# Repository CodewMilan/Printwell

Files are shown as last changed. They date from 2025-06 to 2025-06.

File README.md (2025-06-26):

# Core3D

Core3D is an open-source, budget-friendly CoreXY 3D printer designed for makers who want speed, rigidity,

---

## What’s Inside

CoreXY motion system  
Linear rails on all axes  
Steel + 2020 extrusion frame  
Klipper firmware ready  
Custom-printed brackets and mounts  
BLTouch for mesh leveling  
Fast print speeds on 24V

---

## Sample BOM

Here’s a quick look at some of the core components:

| Component | Description | Qty | Price (PHP) | Price (USD) | Price (INR) |
|---|---|-----|---|---|---|
| Linear Rails | At Least 320mm (THK RSH12ZM) | 3 | 690.00 | $12.07 | 1041.90 |
| Z-Axis Ball Screw Actuator Rail | SG2602A-250H | 1 | 6000.00 | $104.97 | 9060.00 |
| BTT SKR Mini E3 V3 | 3D Printer Controller (32bit) | 1 | 2027.00 | $35.46 | 3060.77 |
| FYSTEC Mini12864 RGB LCD | RGB Neopixel Backlit LCD for 3D Printers | 1 | 393.00 | $6.88 | 593.43 |
| Stepper Motors (NEMA 17, 48mm)  | 3D Printer's Motors (w/ Cables) | 4 | 267.00 | $4.67 | 403.17 |
| 24V 16.7A 400W Power Supply | A compact PSU | 1 | 475.00 | $8.31 | 717.25 |
| Dual Gear Drive Extruder (Clone)| Bontech dual gear extruder clone | 1 | 318.00 | $5.56 | 480.18 |
| Capricorn PTFE Tube (Set) | PTFE Tube for Bowden setups | 1 | 176.00 | $3.08 | 265.76 |
| Heatbed (Ender 3) | 235x235 24V Ender 3 Heatbed | 1 | 875.00 | $15.31 | 1321.25 |
| Heatbed Knob Set | Bolts & nuts for the heatbed | 1 | 132.00 | $2.31 | 199.32 |
| V6 Hotend Set (E3D Clone) | Classic standard hotend | 1 | 343.00 | $6.00 | 517.93 |
| V6 Hotend Aluminum Bracket | Bracket for the V6 Hotend | 1 | 101.00 | $1.77 | 152.51 |
| CHT 0.4mm Nozzle (Clone) | High-speed nozzle upgrade | 1 | 205.00 | $3.59 | 309.55 |
| Endstop Limit Switches | Standard limit switch | 3 | 85.00 | $1.49 | 128.35 |
| 4010 24V Cooling Fan | Blower fan for part cooling | 1 | 92.00 | $1.61 | 138.92 |
| GT2 Timing Belt (Set) | 3m belt set for 3D printers | 2 | 90.00 | $1.57 | 135.90 |
| 20T Stepper Pulley (GT2) | For 5mm shaft steppers | 2 | 44.00 | $0.77 | 66.44 |
| 16T Idler Pulley (GT2) | CoreXY pulley, 3mm bore | 6 | 34.00 | $0.59 | 51.34 |
| 16T Smooth Idler Pulley (GT2) | CoreXY pulley, 3mm bore | 2 | 41.00 | $0.72 | 61.91 |
| 5mm Coupler | For Z Rail and NEMA 17 | 1 | 29.00 | $0.51 | 43.79 |
| M3 Threaded Heat Insert Set | For metal threads in plastic | 1 | 131.00 | $2.29 | 197.81 |
| M3 Washer Set | Basic M3 washers | 1 | 18.00 | $0.31 | 27.18 |
| 1x1" Steel Tubular | 6m of 1x1" steel tubing | 1 | 220.00 | $3.85 | 332.20 |
| 1" Steel Flatbar | 6m of 3mm thick flat steel | 1 | 150.00 | $2.62 | 226.50 |
| 2020 Aluminum Profile | 320mm extrusion | 1 | 196.00 | $3.43 | 295.96 |
| 2020 M3 T-Slot Nuts (Set) | M3 nuts for 2020 extrusion | 1 | 54.00 | $0.94 | 81.54 |
| Generic ABS Filament | ABS spool | 1 | 550.00 | $9.62 | 830.50 |
| TriangleLabs Volcano CHC Hotend | High speed 120W hotend | 1 | 1594.00 | $27.89 | 2406.94 |
| 0.4mm Volcano CHT Nozzle | High-flow nozzle for Volcano | 1 | 123.00 | $2.15 | 185.73 |
| BL-Touch Bed Levelling Sensor | For mesh leveling | 1 | 561.00 | $9.81 | 847.11 |
| PowerHouse Mig Welder | Budget IGBT MIG welder | 1 | 5580.00 | $97.62 | 8425.80 |
| Travon 7" Cutoff Tool | Budget cut-off tool | 1 | 2365.00 | $41.38 | 3571.15 |
| Hand Tap Set | For threading metal | 1 | 173.00 | $3.03 | 261.23 |

**Subtotal:** $305.14

---

## Firmware

Core3D runs on **Klipper** for speed and precision.

---

## pictures

 
 


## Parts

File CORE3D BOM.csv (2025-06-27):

3D Printer Components |  |  |  |  |  |  | x
Component | Description | Qty | Price (PHP) | Price (USD) | Link 1: | Price (INR) | x
Linear Rails | At Least 320mm (THK RSH12ZM) | 3 | 690.00 | $12.07 | https://www.e-gizmo.net/ | 1041.9 | x
Z-Axis Ball Screw Actuator Rail | SG2602A-250H | 1 | 6,000.00 | $104.97 | https://www.e-gizmo.net/ | 9060 | x
BTT SKR Mini E3 V3 | 3D Printer Controller (32bit) | 1 | 2,027.00 | $35.46 | https://shopee.ph/BIGTREETECH-BTT-SKR-MINI-E3-V3.0-32-Bit-Motherboard-Onboard-TMC2209-UART-3D-Printer-Parts-for-Ender3-Ender5-CR10-3D-Printer-i.367074809.2095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 | 3060.77 | x
FYSTEC Mini12864 RGB LCD | RGB Neopixel Backlit LCD for 3D Printers | 1 | 393.00 | $6.88 | https://shopee.ph/S-Mini12864-V3.0-12864-GLCD-Liquid-Crystal-Screen-Mini-Lcd12864-Display-Controller-3D-Printer-LCD-M-i.1144147547.25758436024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 | 593.43 | x
Stepper Motors (NEMA 17, 48mm) | 3D Printer's Motors (w/ Cables) | 4 | 267.00 | $4.67 | https://shopee.ph/Stepper-Nema-17-Bipolar-42mm-Motor-i.20469516.827036167 | 403.17 | x
24V 16.7A 400W Power Supply | A compact PSU | 1 | 475.00 | $8.31 | https://shopee.ph/AC190V-240V-Ultrathin-LED-Power-Supply-DC12V-24V-Mute-Lighting-Transformers-60W-100W-150W-200W-300W-400W-LED-Driver-Power-Adapter-i.33324336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 | 717.25 | x
Dual Gear Drive Extruder (Clone) | The classic Bontech dual gear extruder clone | 1 | 318.00 | $5.56 | https://shopee.ph/R*-Upgraded-Replacement-Aluminum-MK8-Extruder-Feeder-Drive-1.75mm-for-CR-10-CR-10S-Ender-3-Ender-3-PRO-(Red-Dual-Gear)-i.240553168.214355699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 | 480.18 | x
Capricorn PTFE Tube (Set) | PTFE Tube With Great Tolerance For Bowden | 1 | 176.00 | $3.08 | https://shopee.ph/3D-Printer-Kit-with-for-Capricorn-Premium-XS-Bowden-Tubing-1M-PTFE-Tube-for-Ender-3-3-Pro-5-CR-10-Series-10S-20-20-Pro-i.367074809.23510218950 | 265.76 | x
Heatbed (Ender 3) | 235x235 24V Ender 3 Heatbed | 1 | 875.00 | $15.31 | https://shopee.ph/MK3-Heatbed-More-220x220-300x200-310x310mm-12V-24V-Upgraded-Aluminum-Heated-Bed-Hotbed-for-3D-Printer-Parts-Impressora-i.727477289.22914290536 | 1321.25 | x
Heatbed Knob Set | Bolts & nuts with handles for the heatbed | 1 | 132.00 | $2.31 | https://shopee.ph/3D-Printer-Parts-Heated-Bed-Spring-Leveling-Kit-Adjustment-Nut-Springs-Screw-Heatbed-Kit-For-CR-10-Ender-3-MK3-hotbed-i.736543756.20909195496 | 199.32 | x
V6 Hotend Set (E3D Clone) | A classic standard with fan (outdated) | 1 | 343.00 | $6.00 | https://shopee.ph/Extruder-3D-V6-Kits-3D-Print-J-Head-Hotend-for-1.75Mm-3Mm-Filament-0.2-0.3-0.4-0.5Mm-Nozzle-12V-Bowden-Long-Distance-i.736543756.17962673814 | 517.93 | x
V6 Hotend Aluminum Bracket | Aluminum Bracket for the V6 Hotend | 1 | 101.00 | $1.77 | https://shopee.ph/-LHG-V6-Hotend-Fixed-Block-Hot-end-Extruder-Holder-Moung-for-3D-Printer-new-i.1020411077.18981599057 | 152.51 | x
CHT 0.4mm Nozzle (Clone) | The perfect nozzle upgrade for faster prints | 1 | 205.00 | $3.59 | https://shopee.ph/2PCS-PTFE-Coated-CHT-Nozzle-E3D-V6-Brass-Non-Stick-Filament-0.3mm-0.4mm-0.8mm-1.2mm-High-Speed-Flow-Nozzles-3D-Printer-Parts-i.736543756.218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 | 309.55 | x
Endstop Limit Switches | The Standard Limit Switch | 3 | 85.00 | $1.49 | https://shopee.ph/10PCS-Micro-Switch-3Pin-NO-NC-Mini-Limit-Switch-5A-250VAC-KW11-3Z-Roller-Arc-lever-Snap-Action-Push-Micro-switches-ibuw-i.787462331.16673095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 | 128.35 | x
4010 24V Cooling Fan | Blower fan for Part Cooling | 1 | 92.00 | $1.61 | https://shopee.ph/Aideepen-Dc-Cooling-Turbine-Fan-Brushless-3d-Printer-Accessories-Blower-5v-12v-24v-4010-Dc-5015-i.837106144.18533869790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 | 138.92 | x
GT2 Timing Belt (Set) | The standard belt for 3D Printers (3m) | 2 | 90.00 | $1.57 | https://shopee.ph/Hot-sale!-2M-Rubber-GT2-6mm-Open-Timing-Belt-Width-6mm-GT2-Belt-for-3D-Printer-i.736543756.12591120084 | 135.9 | x
20T Stepper Pulley (GT2) | Pulley for the steppers (5mm Inner Diameter) | 2 | 44.00 | $0.77 | https://shopee.ph/-LHG-2Pcs-16T-20T-GT2-Timing-Pulley-5-6.35-8mm-Bore-For-Belt-Reprap-3D-Printer-Ppart-new-i.1020411077.21184571735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 | 66.44 | x
16T Idler Pulley (GT2) | Pulley for the CoreXY (3mm Inner Diameter) | 6 | 34.00 | $0.59 | https://shopee.ph/Handsome-GT2-Idler-Timing-Pulley-Bearing-16T-20T-3-5mm-Bore-F-6mm-Belt-Reprap-3D-Printer-NEW-i.1068445778.23782712191 | 51.34 | x
16T Smooth Idler Pulley (GT2) | Pulley for the CoreXY (3mm Inner Diameter) | 2 | 41.00 | $0.72 | https://shopee.ph/Handsome-GT2-Idler-Timing-Pulley-Bearing-16T-20T-3-5mm-Bore-F-6mm-Belt-Reprap-3D-Printer-NEW-i.1068445778.23782712191 | 61.91 | x
5mm Coupler | Coupler for the Z Rail & NEMA 17 Stepper | 1 | 29.00 | $0.51 | https://shopee.ph/Flexible-Shaft-Coupler-D19-L25-Aluminium-Cnc-Stepper-Motor-Connector-Coupling-Durable-i.20469516.923904311 | 43.79 | x
M3 Threaded Heat Insert Set | For adding metal threads on plastic (4x) | 1 | 131.00 | $2.29 | https://shopee.ph/-'100Pcs-M3-Thread-Knurled-Brass-Threaded-Heat-Set-Heat-Resistant-Insert-Embedment-Nut-M3X5X4-for-3D-Printer-Voron-2.4-Etc-i.367074809.22301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 | 197.81 | x
M3 Washer Set | Any M3 washer would do | 1 | 18.00 | $0.31 | https://shopee.ph/50PCS-Stainless-Steel-Flat-Washer-for-Bolts-M3-M4-M5-M6-M8-M10-M12-Flat-Rings-GizmoTools-i.1086609048.21193782940 | 27.18 | x
1x1" Steel Tubular | 6m of 1x1" Steel (1.5mm thick) | 1 | 220.00 | $3.85 | Pamplona Lumber | 332.2 | x
1" Steel Flatbar | 6m of Flat Steel (3mm thick) | 1 | 150.00 | $2.62 | Pamplona Lumber | 226.5 | x
2020 Aluminum Profile | At least 320mm | 1 | 196.00 | $3.43 | https://shopee.ph/1PC-BLACK-2020-European-Standard-Anodized-Aluminum-Profile-Extrusion-100mm-800mm-Length-Linear-Rail-500mm-for-CNC-3D-Printer-i.427023627.215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 | 295.96 | x
2020 M3 T-Slot Nuts (Set) | thicc ones (7x) | 1 | 54.00 | $0.94 | https://shopee.ph/10PCS-T-Sliding-Nut-Zinc-Coated-Plate-20-30-40-45-Series-M3-M4-M5-M6-M8-M10-Aluminum-Thread-i.427023627.21538381523 | 81.54 | x
Generic ABS Filament | My favorite ABS spool | 1 | 550.00 | $9.62 | https://shopee.ph/Artillery-PLA-PETG-Silk-PLA-ABS-NEW-Stock-3D-Printer-Filament-1Kg-PLA-1.75mm-i.32368896.1722366564 | 830.5 | x
TriangleLabs Volcano CHC Hotend (Clone) | 120W 320deg High Speed Hotend | 1 | 1,594.00 | $27.89 | https://shopee.ph/CHC-KIT-Ceramic-heating-core-quick-heating-mini-for-ender-3-V6-hotend-CR10-CR-10-CR-6-SE-mk3s-3d-printer-hotend-i.736543756.22939488143 | 2406.94
0.4mm Volcano CHT Nozzle | The perfect nozzle upgrade for faster prints | 1 | 123.00 | $2.15 | https://shopee.ph/New-Clone-CHT-Volcano-Nozzle-0.4mm-0.6mm-Brass-Nozzles-High-Flow-Three-eyes-Print-Head-For-Ender-3-1.75mm-3D-Printer-Accessories-i.736543756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 | 185.73
BL-Touch Bed Levelling Sensor | For Mesh Bed Levelling | 1 | 561.00 | $9.81 | https://shopee.ph/Trianglelab-Dforce-3D-BL-TOUCH-Sensor-2021-V3-Auto-Bed-Leveling-Sensor-BL-Auto-Touch-Sensor-for-3D-Printer-i.44365765.17565989008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 | 847.11
PowerHouse Mig Welder | The cheapest IGBT Mig welder | 1 | 5,580.00 | $97.62 | https://shopee.ph/POWERHOUSE-MIGWELD-200A-250A-300A-Gasless-MIG-Inverter-IGBT-ARC-Flux-Wire-Welding-Machine-PHWM-i.316771489.7879295407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 | 8425.8 | x
Travon 7" Cutoff Tool | The cheapest cut-off tool | 1 | 2,365.00 | $41.38 | https://shopee.ph/3800W-45degree-angle-Cutting-machine-cut-off-machine-for-metal-wood-cutting-machine-metal-suitable-i.502107606.13107716964 | 3571.15
Hand Tap Set | Used for adding threads on metal. | 1 | 173.00 | $3.03 | https://shopee.ph/user/purchase/order/149619307206208?type=3 | 261.23 | x
 |  |  |  | $0.00 |  | - | x
SUBTOTAL: |  |  | $305.14 |  |  |  | x
 |  |  |  |  |  |  | x
 |  |  |  |  |  |  | x
 |  |  |  |  |  |  | x
 |  |  |  |  |  |  | x
 |  |  |  |  |  |  | x
 |  |  |  |  |  |  | x
 |  |  |  |  |  |  | x
 |  |  |  |  |  |  | x
 |  |  |  |  |  |  | x
 |  |  |  |  |  |  | x
 |  |  |  |  |  |  | x
 |  |  |  |  |  |  | x
 |  |  |  |  |  |  | x
 |  |  |  |  |  |  | x
 |  |  |  |  |  |  | x
 |  |  |  |  |  |  | x
 |  |  |  |  |  |  | x
 |  |  |  |  |  |  | x
 |  |  |  |  |  |  | x
 |  |  |  |  |  |  | x
 |  |  |  |  |  |  | x
PHP to INR Conversion | 1.51 |  |  |  |  |  | x
PHP to USD Conversion: | 57.16 |  |  |  |  |  | x
 |  |  |  |  |  |  | x
 |  |  |  |  |  |  | x
 |  |  |  |  |  |  | x
 |  |  |  |  |  |  | x
 |  |  |  |  |  |  | x
 |  |  |  |  |  |  | x
 |  |  |  |  |  |  | x

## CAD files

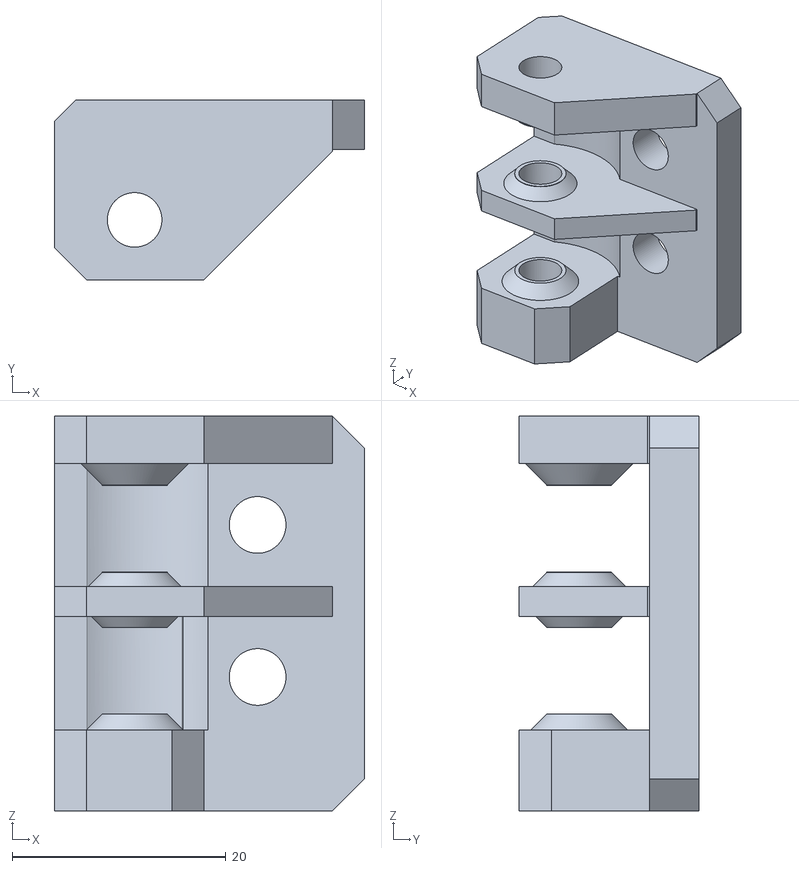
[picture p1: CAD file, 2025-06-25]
Frame/1 X Right_Idler_Mount.stl
29.0 x 16.8 x 36.9

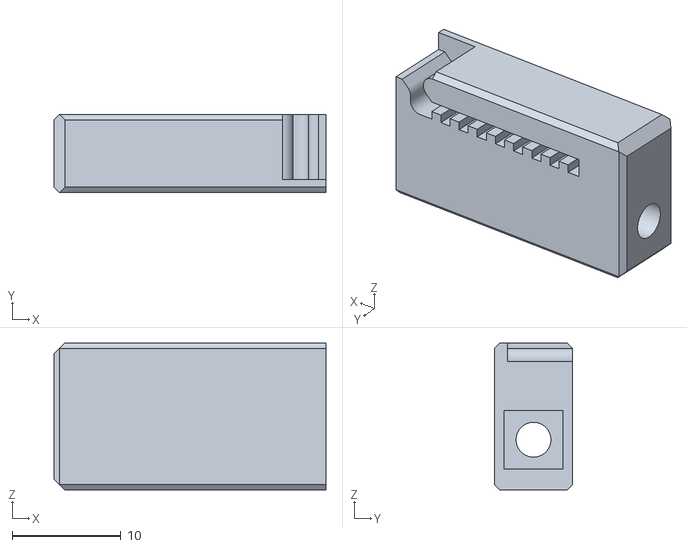
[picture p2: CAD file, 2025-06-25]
X/EVA Correct Belt Tensioner/tension sliders - tension_slider_6mm_belt_M3s_flip_mirror.stl
25.0 x 7.20 x 13.5

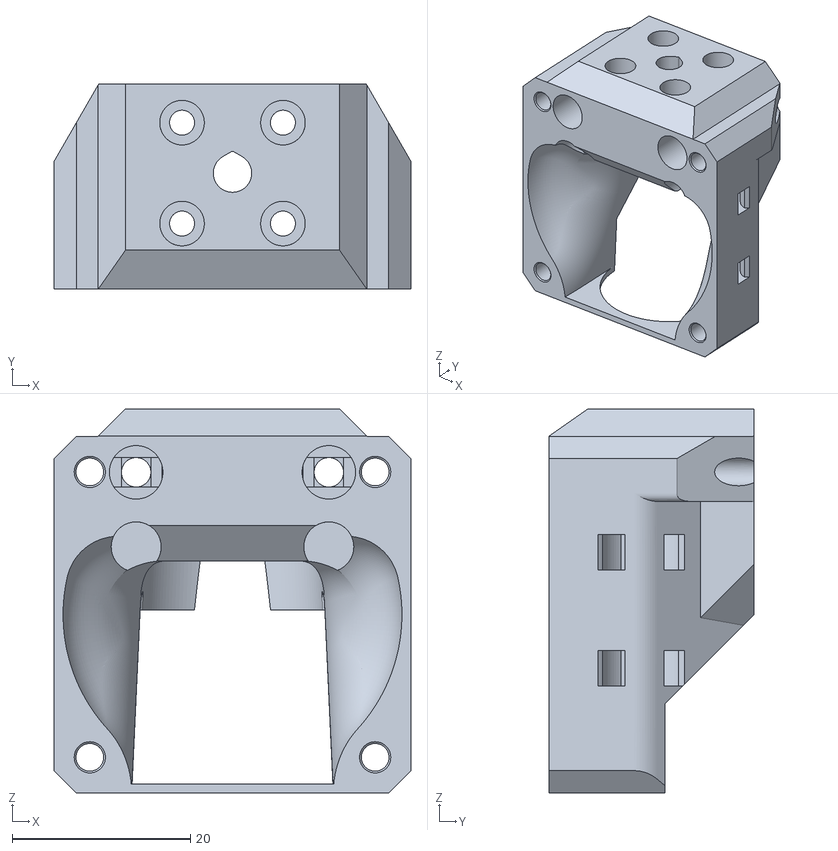
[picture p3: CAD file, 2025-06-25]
X/Klicky/lower_mount.stl
40.0 x 23.0 x 43.1

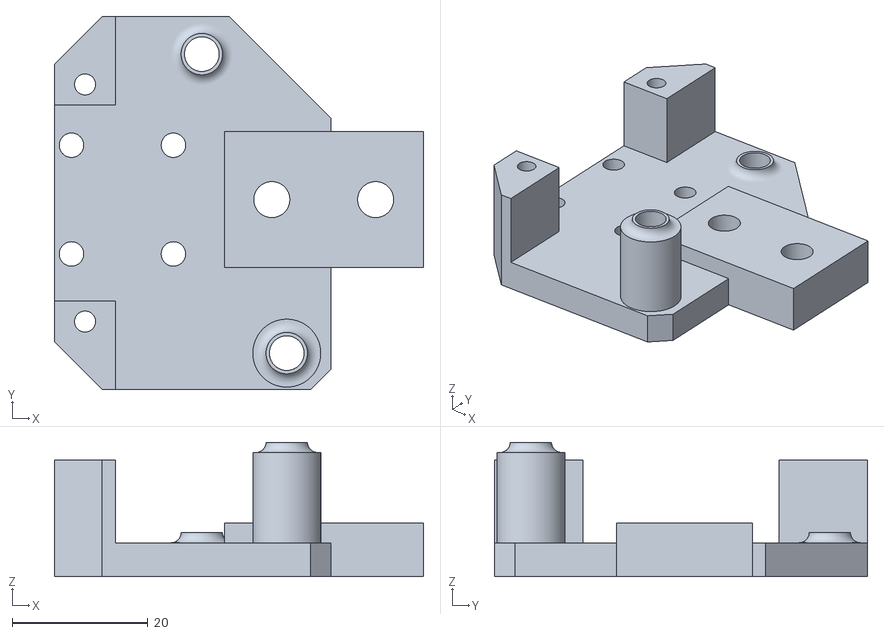
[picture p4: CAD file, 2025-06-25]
Y/1 X Left_Y_Carriage_Bottom.stl
54.3 x 54.9 x 19.8

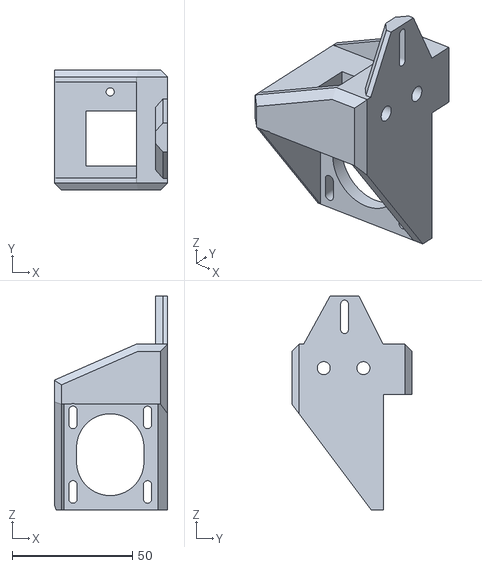
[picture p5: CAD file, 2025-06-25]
Z/1 X Z_Motor_Mount_Right_MK1.stl
47.2 x 50.0 x 89.0

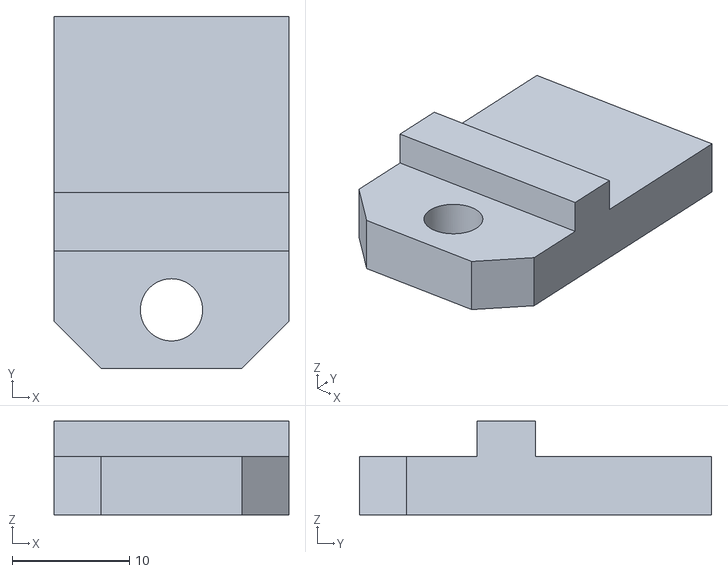
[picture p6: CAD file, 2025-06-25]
Z/330mm Bed/1 x 330_Bed_Mount Rear.stl
20.0 x 30.0 x 8.00

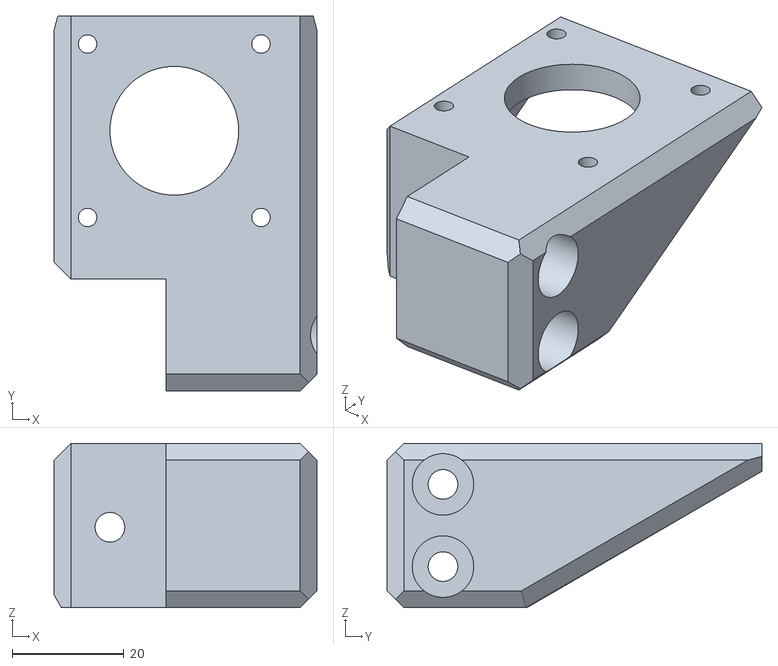
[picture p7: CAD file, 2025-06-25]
Frame/1 X B_Motor_Mount_MK1.stl
47.0 x 67.0 x 29.4

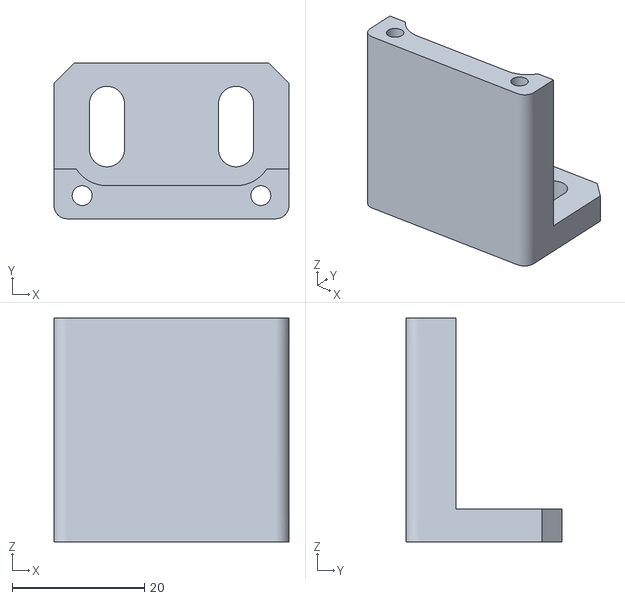
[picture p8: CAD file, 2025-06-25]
X/Klicky/Dock.stl
35.5 x 23.5 x 33.8

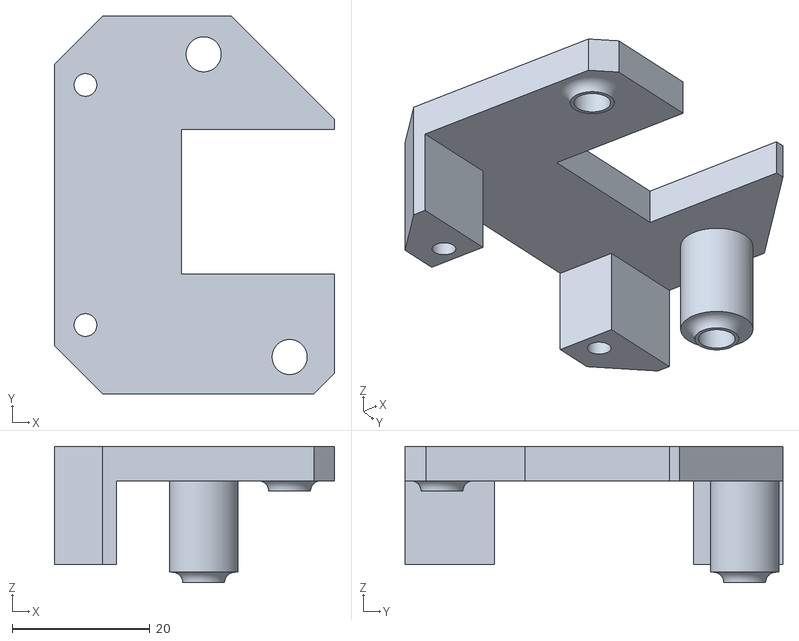
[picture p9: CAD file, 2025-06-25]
Y/1 X Left_Y_Carriage_Top.stl
40.7 x 54.9 x 19.8

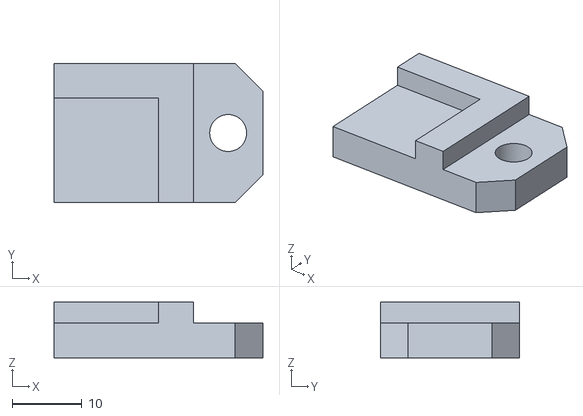
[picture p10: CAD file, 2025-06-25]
Z/330mm Bed/1 x 330_Bed_Mount Left.stl
30.0 x 20.0 x 8.00

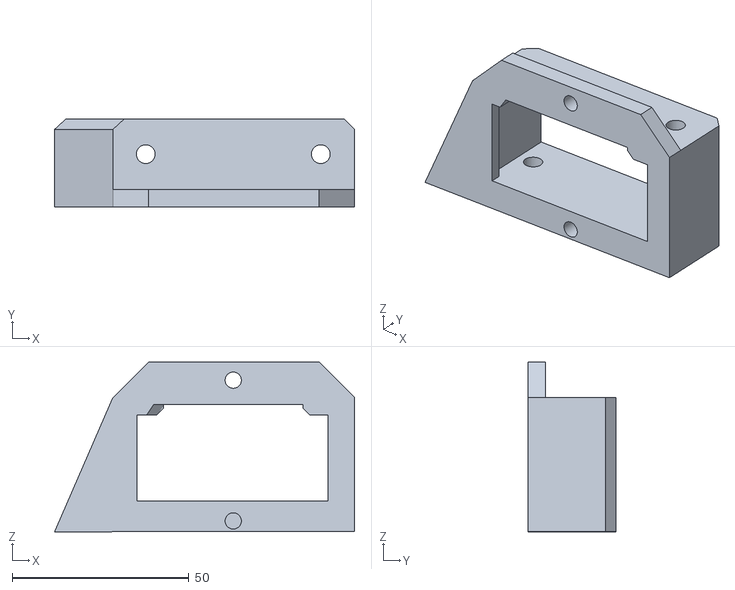
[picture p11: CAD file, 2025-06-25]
Frame/Power_Inlet_Mount.stl
84.8 x 25.0 x 48.0

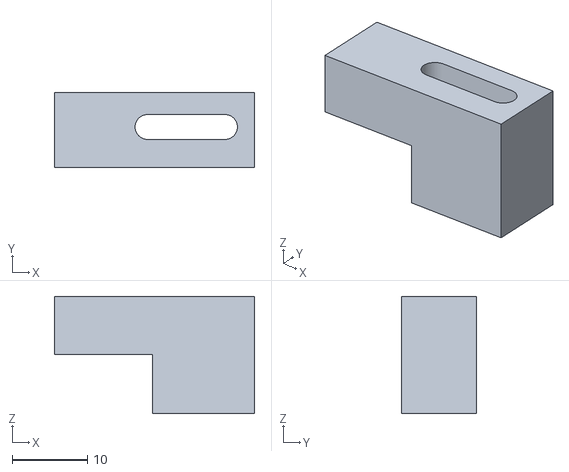
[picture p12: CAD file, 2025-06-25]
Y/1 X Right_X_Endstop_slide.stl
26.5 x 10.0 x 15.6

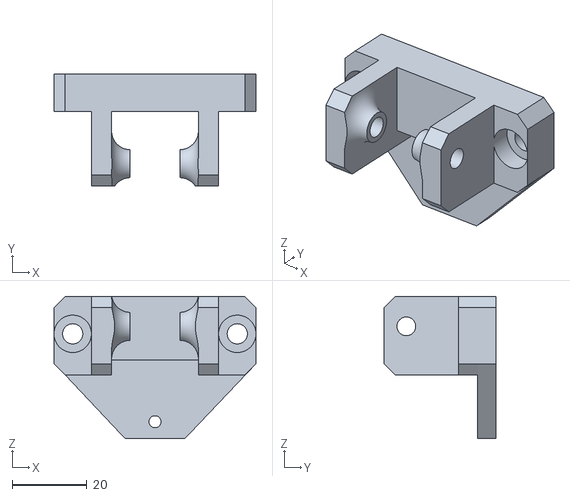
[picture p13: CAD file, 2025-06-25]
Z/3 X Z_Linear_Rail_Top_Mount.stl
54.0 x 30.0 x 38.0

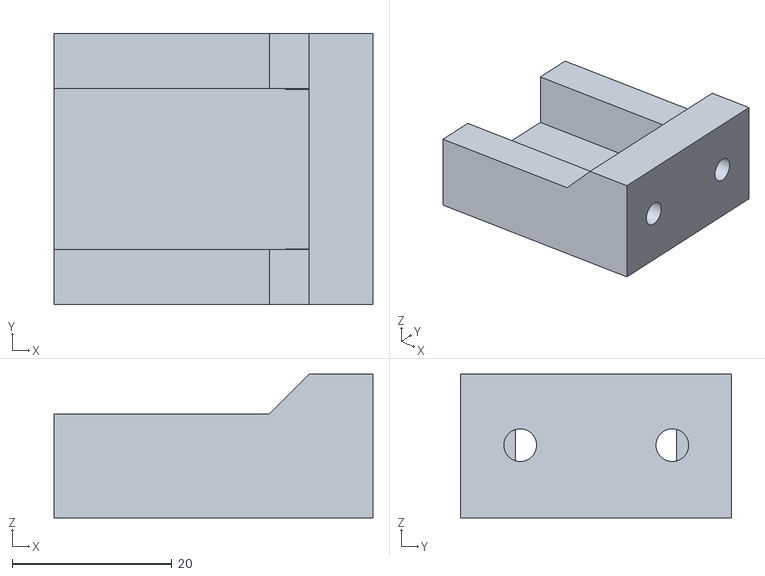
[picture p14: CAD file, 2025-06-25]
Z/330mm Bed/3 X 300mm_Z_Ledge.stl
40.0 x 34.0 x 18.1

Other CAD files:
core3d v1.step
Z/2 X Z_Motor_Mount_Rear_Center_and_Left_MK1.stl
Frame/Foot_Mount.stl
Y/1 X Right_Y_Carriage_Top.stl
Frame/1 X A_Motor_Mount_MK1.stl
Frame/1 X Left_Idler_Mount.stl
Frame/Guide_Tube_Mount.stl
Frame/Rear_PSU_Mount.stl
Frame/Side_PSU_Mount.stl
Y/1 X Right_Y_Carriage_Bottom.stl
Z/3 X Z_Bed_Mount_MG12H.stl
Z/330mm Bed/1 x 330_Bed_Mount Right.stl
core3d v1.f3z

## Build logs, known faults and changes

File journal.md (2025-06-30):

---
title: "Milan's CoreXY Build Log"
author: "Milan"
description: "a cursed journey to building a 3d printer with vibes and sleepless CAD"
created_at: "2025-06-30"
---

**Total Time Spent So Far: 40 Hours**

## **Log 1: CoreXY vs Cartesian Wars**
googled “corexy vs cartesian” and watched videos for hours.  
decided corexy looks cleaner and cooler so i'm doing that.  
folder created: `CoreXY_Build`, and it now contains 40 screenshots and 2 memes.  
**Time Spent: 2 Hours**  
model (1)

---

## **Log 2: Idlers Are a Scam**
found out that idlers need to be aligned perfectly or the belts become noodles.  
sketched something random in Fusion and tried placing 1 X Left_Idler_Mount.stl.  
everything looked okay until i realized nothing was actually constrained.  
**Time Spent: 2 Hours**  
model (2)

---

## **Log 3: Motor Mount Geometry is Black Magic**
placed the A and B motor mounts and tried making them symmetrical.  
fusion 360 said “nah.” had to redo half the sketch.  
ended up with 2 different-looking mounts and prayed they’d work.  
**Time Spent: 2 Hours**  
model (3)

---

## **Log 4: Feet First**
modeled the bottom feet and tested clearances.  
realized my bed might scrape the PSU mount lol.  
redesigned the feet like 4 times.  
**Time Spent: 2 Hours**  

---

## **Log 5: Y-Carriage Confusion**
started mocking up the y-carriage setup.  
couldn’t tell which way was front anymore.  
added dummy blocks for top and bottom.  
**Time Spent: 2 Hours**  
model (4)

---

## **Log 6: The Guide Tube Mount**
decided to add the filament guide path now instead of later.  
made a custom part that looked weirdly like a flute.  
**Time Spent: 1.5 Hours**  

---

## **Log 7: The Endstop Slide Crisis**
wanted to add endstops, forgot to plan their placement.  
made a part called “endstop_slide” and it just floats there.  
works in theory. not tested in the physical realm yet.  
**Time Spent: 1.5 Hours**  
model (5)

---

## **Log 8: Z Motor Woes**
figured out the z-motor position after too long.  
used Right MK1 and Rear+Left combined motor mounts.  
alignment was a pain but at least it looks clean now.  
**Time Spent: 2 Hours**  
model (6)

---

## **Log 9: Power Inlet Engineering**
added a slot for the power inlet, measured nothing, eyeballed everything.  
made it fit using the "move body" tool 14 times.  
**Time Spent: 1 Hour**  
model (7)

---

## **Log 10: Rear PSU Hopes**
decided to go with a rear PSU mount setup.  
modeled the rear PSU mount and started checking airflow paths.  
**Time Spent: 2 Hours**  
model (8)

---

## **Log 11: Belt Path Madness**
tried visualizing the belt loop path.  
rotated gantry components 500 times.  
added mock pulleys and tensioners (they float too).  
**Time Spent: 2 Hours**  
model (9)

---

## **Log 12: X and Y Carriage Mesh**
finally put together both x and y sides of the gantry.  
printed test versions of left/right carriage tops.  
**Time Spent: 2.5 Hours**  
model (10)

---

## **Log 13: Side PSU Mount Exists**
added the side PSU mount. fits awkwardly but i’ll allow it.  
debated moving it again but left it in for now.  
**Time Spent: 1 Hour**  
model (11)

---

## **Log 14: Z Ledges Exist Now**
designed supports to hold the bed plate—ledges for linear rails.  
used 3 identical supports for symmetry.  
**Time Spent: 1.5 Hours**  

---

## **Log 15: Bed Mount Bracket Bravery**
modeled the bed brackets. printed left, right, and rear.  
tweaked holes after first test didn’t align.  
**Time Spent: 2 Hours**  

---

## **Log 16: Internal Cable Path Setup**
ran pretend wires through fusion’s comment boxes.  
figured out tube routing from extruder to hotend.  
**Time Spent: 1 Hour**  

---

## **Log 17: Rear Mount Debugging**
rear left motor mount was slightly off—fixed by mirroring.  
also redesigned the rear top plate to match spacing.  
**Time Spent: 2 Hours**  

---

## **Log 18: Final Folder Chaos**
organized all STL files into named folders.  
renamed half the files to actually make sense.  
made render screenshots and a gif for the gram.  
**Time Spent: 2 Hours**  

---

## **Log 19: Final STL Exports**
cleaned up fusion timeline.  
final export of all 30+ STL files for slicing.  
**Time Spent: 1.5 Hours**  

---

## **Log 20: Writing This Log**
decided i didn’t want to forget how scuffed this journey was.  
writing markdown logs while fusion lags in the background.  
**Time Spent: 1 Hour**


---

**status update: it might work. or explode. but it looks real.**  
printer is coming to life slowly, piece by piece.  
it’s not done yet, but it’s got *soul*.

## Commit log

2025-06-27 Update CORE3D BOM.csv
    [CORE3D BOM.csv]
2025-06-29 Add large F3Z file with LFS
    [core3d v1.f3z]
2025-06-30 added step files
    [core3d v1.step]
